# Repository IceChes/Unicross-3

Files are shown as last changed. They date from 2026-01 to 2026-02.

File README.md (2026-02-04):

# Unicross
Unicross is a highly reliable cross-gantry 3D printer built with accessible parts and simple design practices.



For up to date CAD: https://cad.onshape.com/documents/4eb1484887fc2987f4944e2c/w/5df6581cff3116f0fb19b47b/e/0f43dcdbef88a724da59cfd0

This project is IN PROGRESS and subject to change at any time without notice.

### Features:
- 180mm printing area
- Printable in PETG
- Direct drive extruder and Bambu hotend
- Accessible BOM
- Assembly manual
- Quality part cooling
- Self replicating
- Open source hardware (through Onshape)
- Runs Klipper

### Coming eventually:
- Prusaslicer configs
- Klipper configs
- Wiring guide

# What's the point?
My Unicross 3 build, after ironing out some first-assembly issues, has never broken. Cross gantry 3D printers are known for their speed, yes, but the dead-simple geometry and the overbuilt mechanics of the kinematics system in general makes it an unbelievably reliable basis for a 3D printer. 

# Sourcing components
This isn't a Voron or something that you can just buy a kit for, but the components are really easy to get. Due to tariffs, however, I cannot accurately estimate a price for this machine. 

I do not recommend spending more than $350 to build this thing. It's just not worth it, even with the reliability. I implore you to do your own shopping and come to your own conclusions.

**Cost cutting tips:** 
- If you have a couple old Monoprice Maker Selects lying around (this is a surprisingly common situation?) then the price drops dramatically as many of the motion components (and the bed!) can be repurposed.
- Both X motors must be identical, and both Y motors must be identical. However, the X motors and Y motors don't have to be the same as each other.
- The entire electronics enclosure can be PLA.
- There's a huge list of compatible beds to choose from. Pick any one that will fit! Alternatively, pop into Onshape and design your own - the design is uncomplicated.
- The power supply mounts are designed for an LRS-350-24 from meanwell. However, the Ender 3 power supply is exactly the same size, just thicker.
- Short on LM8LUUs? You can use regular LM8UUs for the Z axis with a small quality sacrifice, just not for the X/Y axes.

# Features, in detail
### X/Y axes
Unicross is based on linear rods due to their low cost and mechanical simplicity. They aren't super rigid or anything, so the machine isn't terribly fast, but it's cheap and it works. The belts are regular GT2 belts.

### Z axis
The Z axis is a single-motor dual-screw system driven with a belt. This isn't perfect, but it gets Z axis quality that's up to my standards. 

### Electronics
It has them. Requires bending pins for assembly, but it's not actually that big of a deal.

### Toolhead
The toolhead is a very simple plastic brick, designed for simplicity and durability. There isn't much to say here. 

# Questions you may have
### I don't like something. Can it be changed?
Sure. Just copy the Onshape document or download the assembly STEP and make whatever changes you want. I would love if you'd also DM me @iceches on Discord and I'll see if I can implement it in the main repository.

### What can I print?
PLA, PETG, TPU without an enclosure. If you have an enclosure or you cover up the sides and top, ABS, ASA, and PA are also printable.

### What can't I print?
I have no idea. Every filament I've tried has worked.

### Are there any known issues with this design?
Certainly. The idler mounting is suboptimal, and the Z axis is imperfect. I was unable to fix these two issues, but you might be able to!

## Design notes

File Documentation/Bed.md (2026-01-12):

# Bed stuff 
Unicross 3 was originally designed to use the Kingroom KP3S bed. However, this printer is discontinued. Some alternatives have been offered instead.
- Kingroon KP3S: The original bed. The PID tuning will work out of the box.
- Custom Unicross: Custom 200W PCB bed. Gerber files included. See documentation below.
- Lerdge IX: 180mm bed from the little-known Lerdge IX printer. These are pretty cheap online.
- Monoprice: Monoprice Maker Select bed. Oversized, but very common. Uses 12 volts, however, so some PID tuning may be in order.

### Notes
The BOM assumes that you have ALL necessary mounting hardware and electronics. This means that if you are using, for example, the custom Unicross bed, you will need to supply your own long M3 bolts, springs, and knobs. 
All Unicross beds MUST be able to be leveled using springs.
Also, remember to print the cooresponding mounts for whatever bed you pick.

### Custom bed
The custom Unicross bed is not a particularly economical option due to the cost of one-off manufacturing of boards this large. However, it is by far the most powerful bed.

The PCB has been designed for 1oz copper. It should be ordered in as thick of an FR4 substrate as reasonable, or ~3mm aluminum substrate. 

Kicad and gerber files are attached in the /Files/Bed Files/ directory.

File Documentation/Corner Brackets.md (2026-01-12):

# Unicross Corner Brackets
Unicross uses a variety of 90-degree angle corner brackets to secure various parts of the machine. The user is given the choice between large and small brackets.

There are a total of 12 corner brackets.
- 4 for the base. They support the vertical extrusions at the front of the machine.
- 4 for the sides. They support the Z axis side rails.
- 4 for the top. They brace the top of the printer.

Of these, the 8 for the base and the sides can be large or small. The top brackets **MUST** be large brackets, or you will risk the machine being pulled out of square, resulting in all kinds of artifacts.

The 4 for the base _should_ be large brackets, as this will help give stability to the entire machine. The back side of the printer is not as rigid as the front due to its construction, but further reinforcing the front will still help the back quite a lot.

The 4 for the side rails can be large or small. Large brackets will marginally improve rigidity, but small ones save you a couple bolts. 

TL;DR I recommend printing 8 large corner brackets and 4 small ones.

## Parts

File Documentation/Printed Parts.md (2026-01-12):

# Unicross 3 Printed Parts guide
This is an extensive guide on printing the Unicross 3 components. 

---

# Print settings
Assuming 0.3mm layer height and 0.4 nozzle.

### Minimal structural settings for ABS
- 3 walls
- 4 top layers
- 4 bottom layers
- 20% 3D infill

### Minimal structural settings for PETG
- 5 walls
- 6 top layers
- 6 bottom layers
- 25% 3D infill

### Nonstructural settings for all filaments
- 3 walls
- 3 top layers
- 2 bottom layers
- 10% any infill

I highly recommend enabling the option in your slicer that adds a sparse top layer before the true top layer printing starts. This will dramatically improve panel quality.

**Settings for other filaments are up to the user's discretion to decide.**

### Bed Mounts (all)
- Quantity: 2 (of your selected mount)
- Settings: At least minimal structural settings
- Filament: Recommended ABS or PETG, or another non-creeping filament resistant to 70C or so

### Jigs (all)
- Quantity: 1 of each item
- Settings: Nonstructural
- Filament: Any

Jigs are disposable.

### Panels - all except screw plates and fan retainer
- Quantity: 1 of each item
- Settings: Nonstructural
- Filament: Any

### Panels - fan retainer
- Quantity: 1
- Settings: 100% infill solid
- Filament: Any

### Panels - screw plates
- Quantity:
  - 4x 2mm-2x1
  - 2x 2mm-2x2
  - 2x 4mm-2x1
  - 2x 4mm-2x2
- Settings: 100% infill solid
- Filament: Any

### Toolhead - toolhead block
- Quantity: 1
- Settings: At least minimal structural settings
- Filament: Recommended ABS or PETG, or another non-creeping filament resistant to 70C or so

### Toolhead - toolhead hotend clamp
- Quantity: 1
- Settings: At least minimal structural settings
- Filament: Recommended ABS or PETG, or another non-creeping filament resistant to 70C or so

### Toolhead - BLTouch mount
- Quantity: 1
- Settings: 100% infill solid
- Filament: Any filament resistant to 70C

### Fastening plate
- Quantity: 11 recommended, but you can bolt these on in loads of places
- Settings: 100% infill solid
- Filament: Any non-creeping filament

### Front foot
- Quantity: 2
- Settings: At least minimal structural settings
- Filament: Any non-creeping filament

### IEC socket mount
- Quantity: 1
- Settings: Nonstructural
- Filament: Any

### Idler bracket
- Quantity: 4
- Settings: 100% infill solid
- Filament: Any non-creeping filament

### Idler cover
- Quantity: 4
- Settings: At least minimal structural settings
- Filament: Any

### Large corner bracket
- Quantity: See bracket guide
- Settings: 100% infill solid
- Filament: Any non-creeping filament

### Long mount
- Quantity: 2
- Settings: At least minimal structural settings
- Filament: Recommended ABS or PETG, or another non-creeping filament resistant to 70C or so

### PSU fan duct (optional part)
- Quantity: 1
- Settings: Nonstructural
- Filament: Any

### Rear foot
- Quantity: 2
- Settings: At least minimal structural settings
- Filament: Any non-creeping filament

### Rod block with zip tie
- Quantity: 1
- Settings: At least minimal structural settings
- Filament: Any non-creeping filament

### Rod block
- Quantity: 3
- Settings: At least minimal structural settings
- Filament: Any non-creeping filament

### Short mount
- Quantity: 2
- Settings: At least minimal structural settings
- Filament: Recommended ABS or PETG, or another non-creeping filament resistant to 70C or so

### Small corner bracket
- Quantity: See bracket guide
- Settings: 100% infill solid
- Filament: Any non-creeping filament

### Z motor mount
- Quantity: 1
- Settings: At least minimal structural settings
- Filament: Recommended ABS or PETG, or another non-creeping filament resistant to 70C or so

### Z rod top support
- Quantity: 4
- Settings: At least minimal structural settings
- Filament: Any non-creeping filament

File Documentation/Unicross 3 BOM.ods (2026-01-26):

Framing and Hardware
Part | Description | Quantity | Notes
350mm 2020 extrusion | Primary frame component | 14 | You can also buy 5 meters and cut it into 14 sections, with an extra 100mm piece.
M5x10 button head cap screw |  | 150 | You'll have some extra of all major hardware components, these are approximations.
M5 T nut |  | 150
M3x10 button head cap screw |  | 75
M3 square nut |  | 75
M3x12 button head cap screw | Extruder + fan screws | 4 | Exact quantity. Specifically to mount the sherpa mini and the hotend fan. May come included with both!
M4x8 button head cap screw | PSU screws | 4 | Exact quantity.
M3x25 button head cap screw | Tensioner + hotend screws | 6 | Exact quantity. Used for mounting the tensioners and also the hotend. You may get 2 with your hotend.
M5x25 button head cap screw | Idler retaining bolts | 4 | Exact quantity.
Electronics
Part | Description | Quantity | Notes
Raspberry Pi model B | Any model-B Pi-shaped SBC | 1 | I use a Pi 4, but the SBC market is the wild west nowadays.
BTT SKR Pico | Mainboard | 1
Stepper motor | NEMA17 of ~40mm in length | 5 | I do not recommend any particular motor, use spares if you have them. HOWEVER the XY motors should all be the same.
Stepper cable |  | 5 | Don't forget!
Stepper splitter | Run motors in parallel | 2
Meanwell LRS-350-24 | Generic power supply | 1 | If you have an Ender PSU or whatever that works too, but it won't sit flush with the panels.
IEC 320 switched + fused socket | Power plug | 1 | You want the kind with the mounting holes on the top and bottom, not the left and right.
Z Axis
Part | Description | Quantity | Notes
8x250mm linear rod | Z axis rods | 4
30T GT2 pulley | Z axis pulleys | 2
~730mm GT2 belt loop | Z belt | 1 | Exact belt length is 727mm, but the belt should be slightly longer.
250mm T8 leadscrew | Z screw | 2 | PLEASE try to get straight screws.
T8 nut | Z screw nut | 2 | The round ones!
608 bearing | Screw bearings | 2 | Yep. Those.
Bed |  | 1 | Read Bed.md for information
X and Y Axes
Part | Description | Quantity | Notes
8x300mm linear rod | Gantry and cross rods | 6
20T GT2 pulley | Primary pulleys | 4 | All 20T GT2 hardware can be substituted for 16T if you'd like.
20T GT2 idler | Primary idlers | 4
GT2 belt |  | 4x700mm
LM8LUU bearing | Linear bearings | 10 | 4 of these will be used on the Z axis, and 2 will be used on the toolhead.
Toolhead
Part | Description | Quantity | Notes
Bambu Lab X/P/A hotend | Hotend | 1
2510 axial fan | Hotend cooling fan | 1 | Try to get one included with the hotend, but make sure it has a normal connector.
4010 blower fan | Part cooling fan | 3 | You'll need an extra for electronics cooling.
BLTouch-style probe | Probe | 1 | If it ain't broke...
Sherpa mini | Extruder | 1
PTFE tubing |  | ~40mm | Cut to length during head assembly.

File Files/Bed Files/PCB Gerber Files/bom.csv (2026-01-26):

Designator | Footprint | Quantity | Value | LCSC Part #
J1, J2 | SolderWire-1.5sqmm_1x01_D1.7mm_OD3.9mm | 2 | Conn_01x01

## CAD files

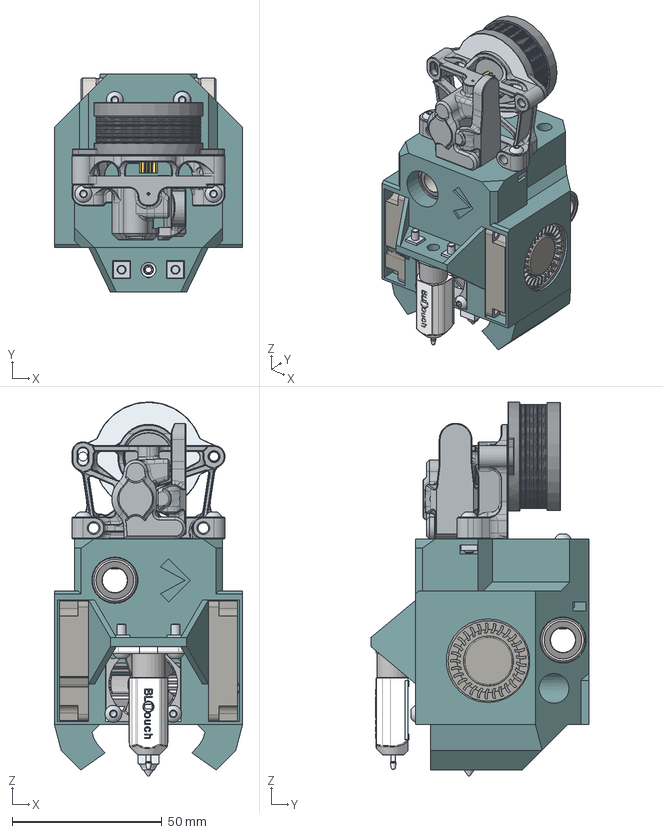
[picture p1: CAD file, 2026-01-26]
Files/Assemblies/Toolhead.step
63.0 x 73.0 x 125.1 mm
Socket button head screw M3x0.5 x 12 x 2
4010 Blower x 2
Square thin nut grade B M3x0.5 x 8
Socket button head screw M3x0.5 x 10 x 6
Socket button head screw M3x0.5 x 20 x 2
25MM SUNON FAN x 2
Sherpa Mini
Hotend
Toolhead Block
LM8LUU x 2
ProbePin
Housing
BreadBoard
CoilBL

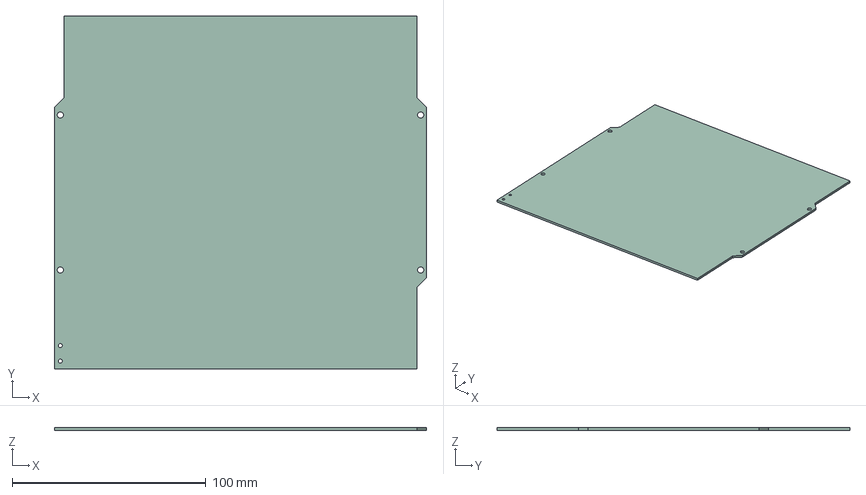
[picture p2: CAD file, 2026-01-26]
Files/Bed Files/Unicross Bed.step
192.0 x 182.0 x 1.60 mm

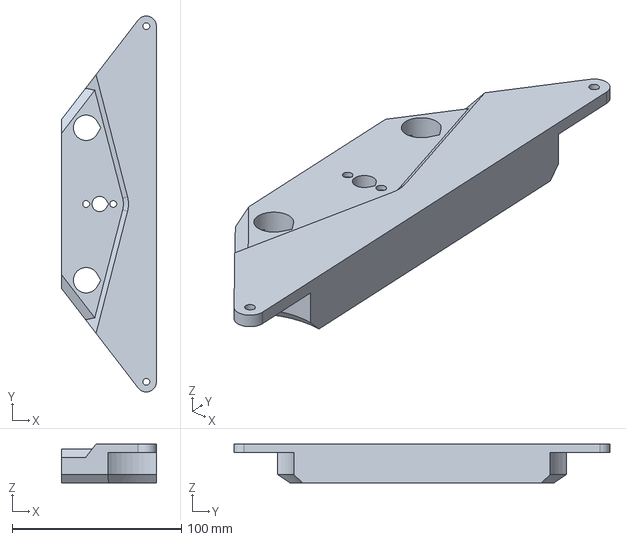
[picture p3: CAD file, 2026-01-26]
Files/Individual Part STEPs/Bed Mounts/Bed Mount - Monoprice.step
56.0 x 222.0 x 23.0 mm

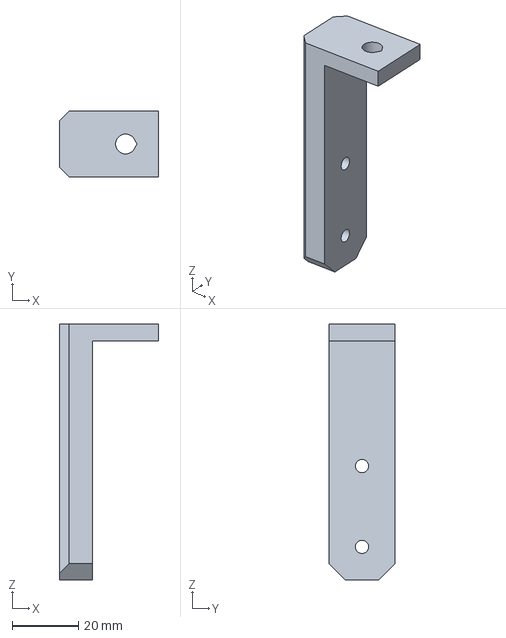
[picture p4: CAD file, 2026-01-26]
Files/Individual Part STEPs/Jigs/Jigs - Drill Jig.step
30.0 x 20.0 x 77.3 mm

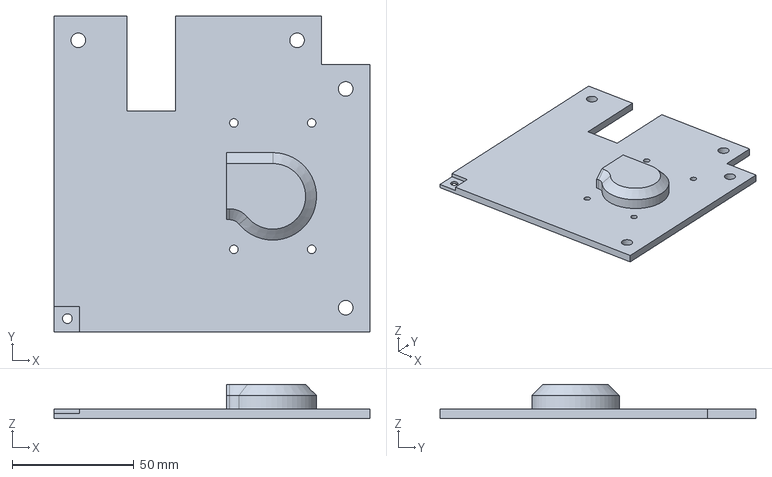
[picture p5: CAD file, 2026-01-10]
Files/Individual Part STEPs/Panels/Back Right Top Plate.step
130.0 x 130.0 x 14.0 mm

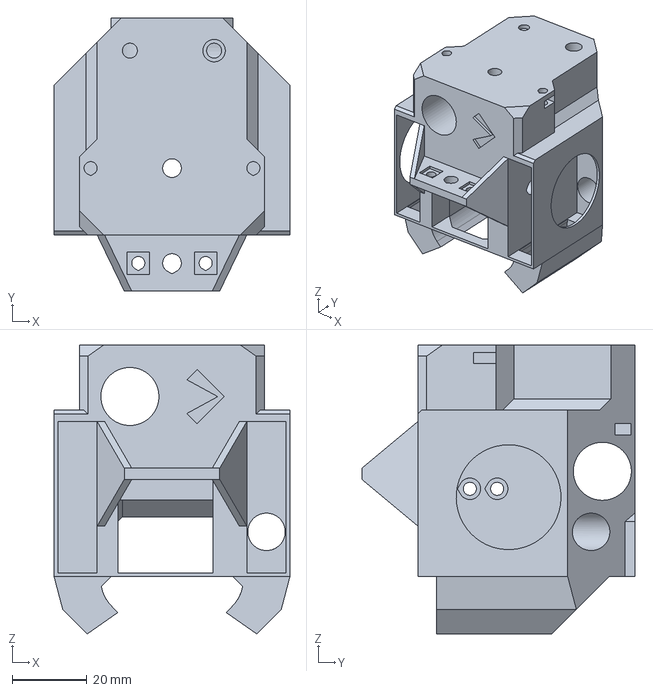
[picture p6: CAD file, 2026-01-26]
Files/Individual Part STEPs/Toolhead Block.step
63.0 x 73.0 x 77.2 mm

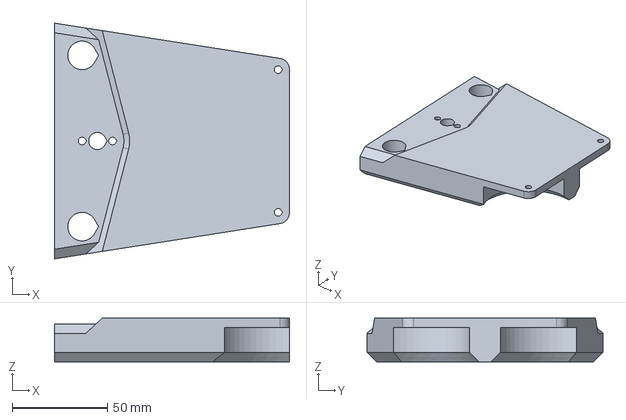
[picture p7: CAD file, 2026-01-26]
Files/Individual Part STEPs/Bed Mounts/Bed Mount - Lerdge IX.step
123.5 x 123.9 x 23.0 mm

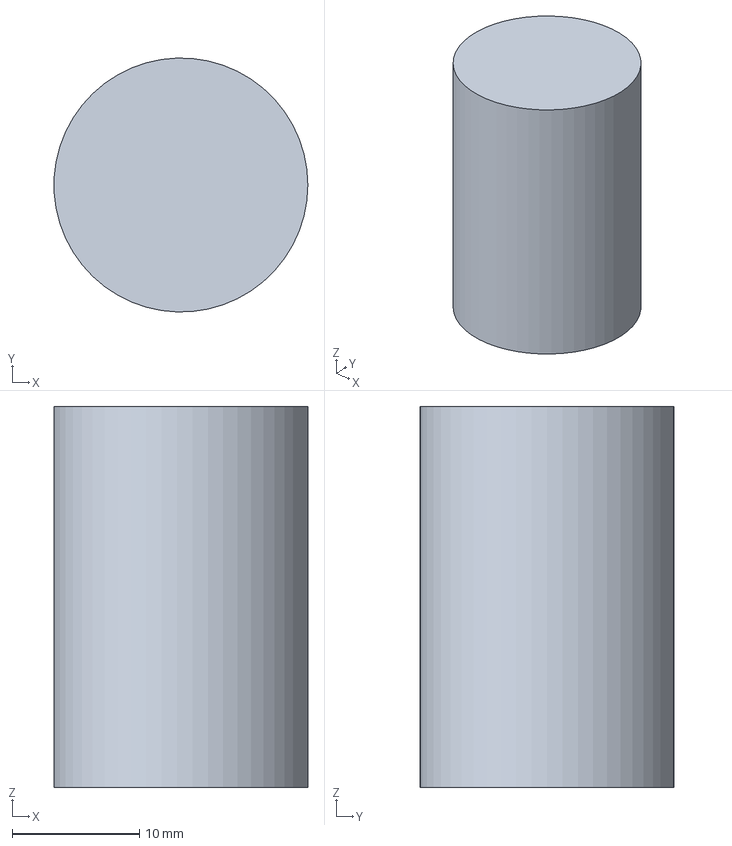
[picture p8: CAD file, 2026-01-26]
Files/Individual Part STEPs/Jigs/Jigs - Bearing Tool.step
20.0 x 20.0 x 30.0 mm

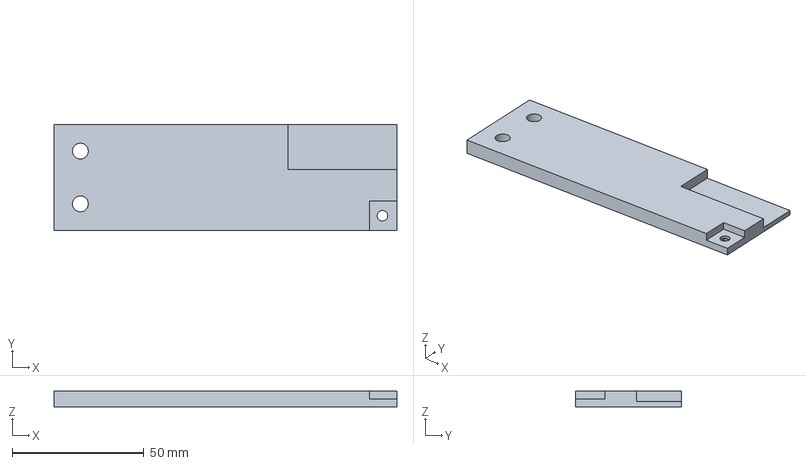
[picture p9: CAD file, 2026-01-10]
Files/Individual Part STEPs/Panels/Front Left Bottom Plate.step
130.0 x 40.0 x 6.00 mm

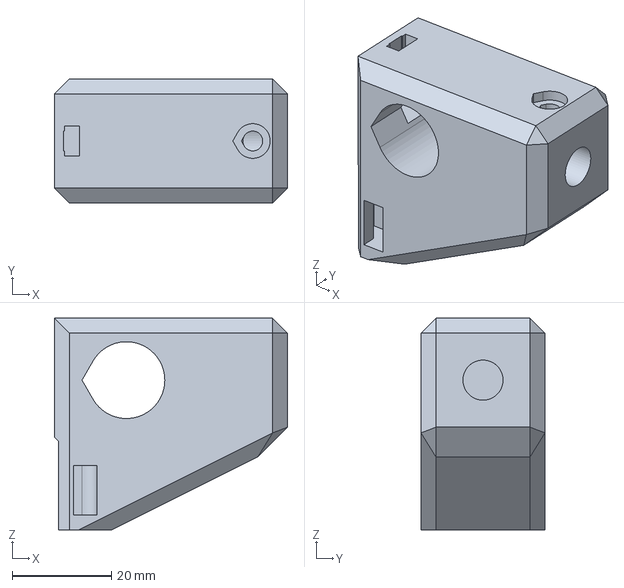
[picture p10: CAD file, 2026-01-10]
Files/Individual Part STEPs/Rod Block.step
47.0 x 25.0 x 42.7 mm

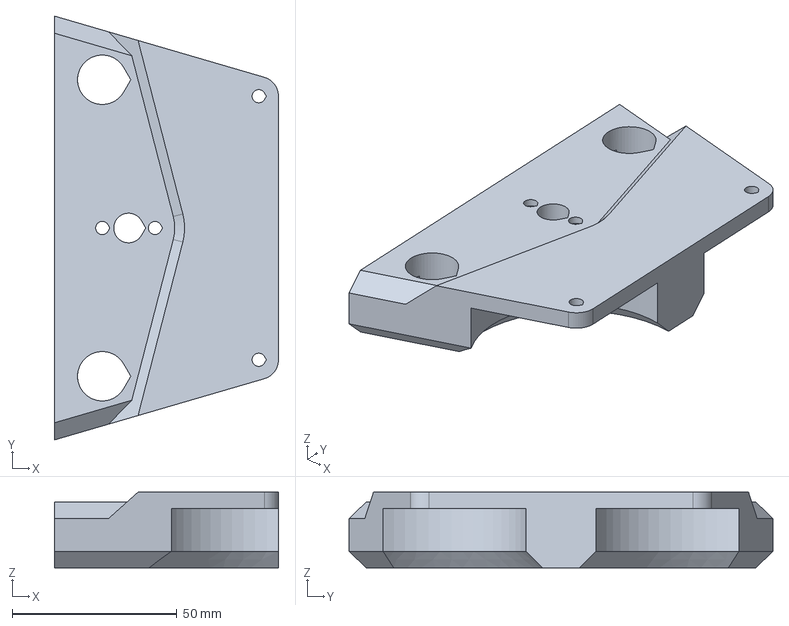
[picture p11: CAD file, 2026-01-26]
Files/Individual Part STEPs/Bed Mounts/Bed Mount - Custom Unicross.step
68.0 x 128.7 x 23.0 mm

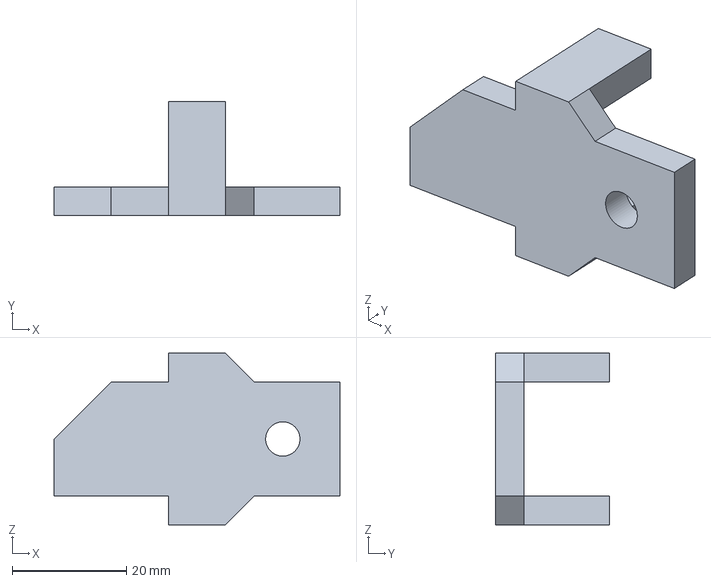
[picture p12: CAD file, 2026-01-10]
Files/Individual Part STEPs/Idler Cover.step
50.0 x 20.0 x 30.0 mm

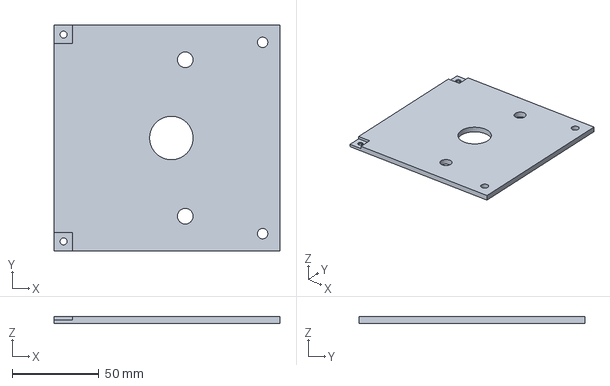
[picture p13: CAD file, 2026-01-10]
Files/Individual Part STEPs/Panels/Right Mid Top Plate.step
130.0 x 130.0 x 4.00 mm

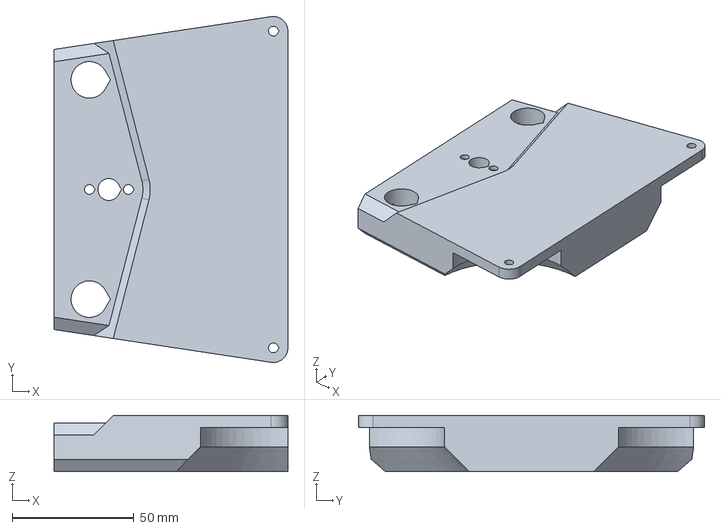
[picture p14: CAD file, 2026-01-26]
Files/Individual Part STEPs/Bed Mounts/Bed Mount - KP3S.step
96.0 x 142.0 x 23.0 mm

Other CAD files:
Files/Individual Part STEPs/Fastening Plate.step
Files/Individual Part STEPs/Panels/Front Right Top Plate.step
Files/Individual Part STEPs/Panels/Left Mid Top Plate.step
Files/Individual Part STEPs/Small Corner Bracket.step
Files/Bed Files/Unicross Bed.dxf
Files/Individual Part STEPs/Front Foot.step
Files/Individual Part STEPs/IEC Socket Mount.step
Files/Individual Part STEPs/Idler Bracket.step
Files/Individual Part STEPs/Large Corner Bracket.step
Files/Individual Part STEPs/Long Mount.step
Files/Individual Part STEPs/PSU Fan Duct.step
Files/Individual Part STEPs/Panels/2x1 Screw Plate - 2mm.step
Files/Individual Part STEPs/Panels/2x1 Screw Plate - 4mm.step
Files/Individual Part STEPs/Panels/2x2 Screw Plate - 2mm.step
Files/Individual Part STEPs/Panels/2x2 Screw Plate - 4mm.step
Files/Individual Part STEPs/Panels/Back Left Bottom Plate.step
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

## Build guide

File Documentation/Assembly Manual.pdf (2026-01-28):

You’re going to need to prep 4 extrusions before use. Find them, an M5 tap, a 3mm drill bit, and the drill jig.

Tap the hole at the end. Repeat for the other 3.

Attach the jig to the end of an extrusion and drill a hole using the top hole of the jig. Repeat for the other 3.

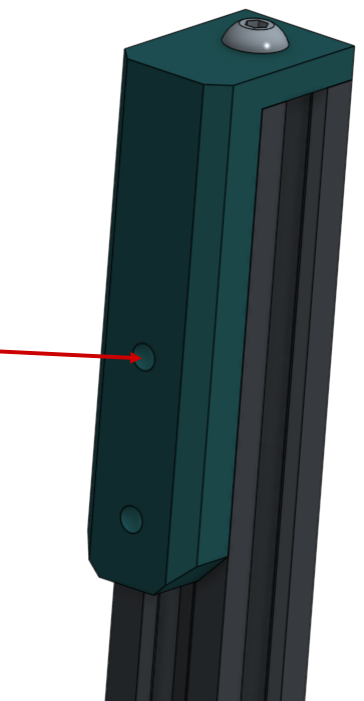
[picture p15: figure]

Attach the jig again at a 90 degree offset and drill through the bottom hole. Repeat for all 3.

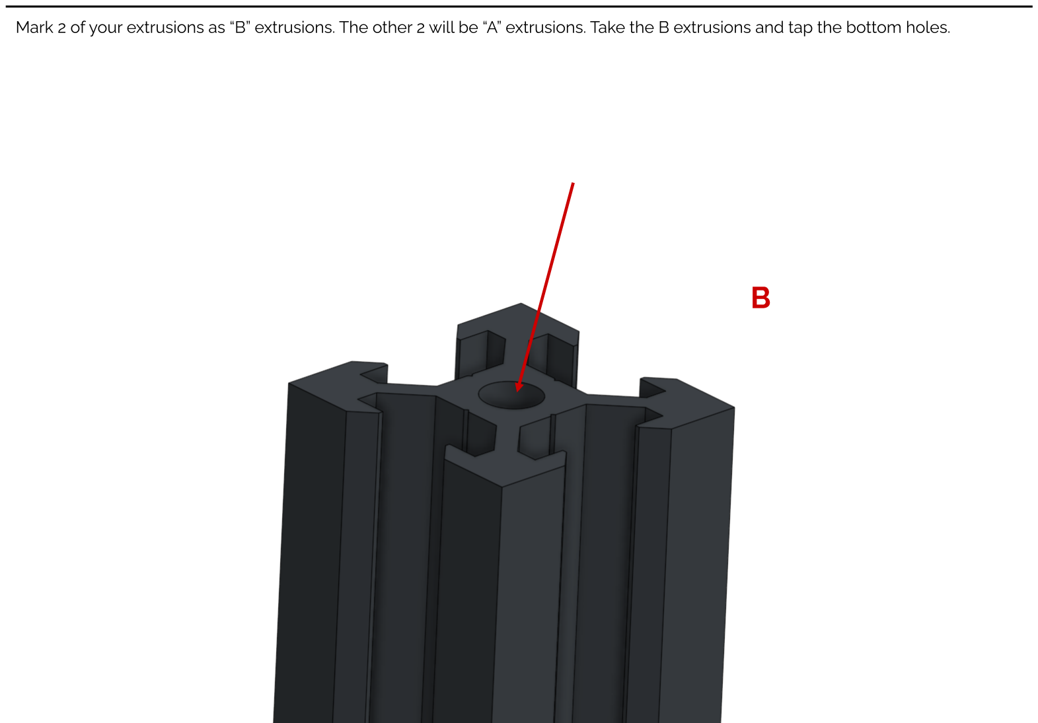
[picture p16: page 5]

Mark 2 of your extrusions as “B” extrusions. The other 2 will be “A” extrusions. Take the B extrusions and tap the bottom holes.

B

Mark 2 of your extrusions as “B” extrusions. The other 2 will be “A” extrusions. Take the B extrusions and tap the bottom holes.

B

M3 square nut | 4
M3x10 screw | 4
Rear left bottom plate | 1
Rear foot | 1

M3 square nut | 4
M3x10 screw | 4
Rear right bottom plate | 1

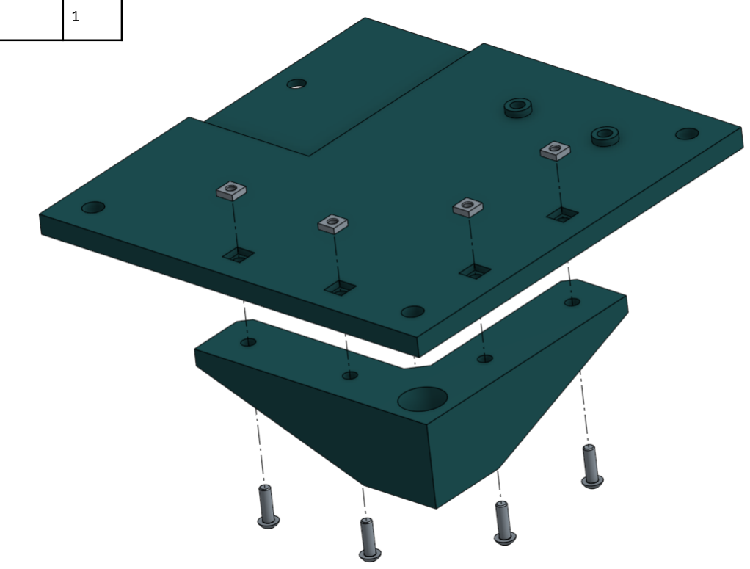
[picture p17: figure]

Rear foot | 1

2020 extrusion | 4 | Arrange 3 extrusions edge to edge on a flat surface in this orientation.

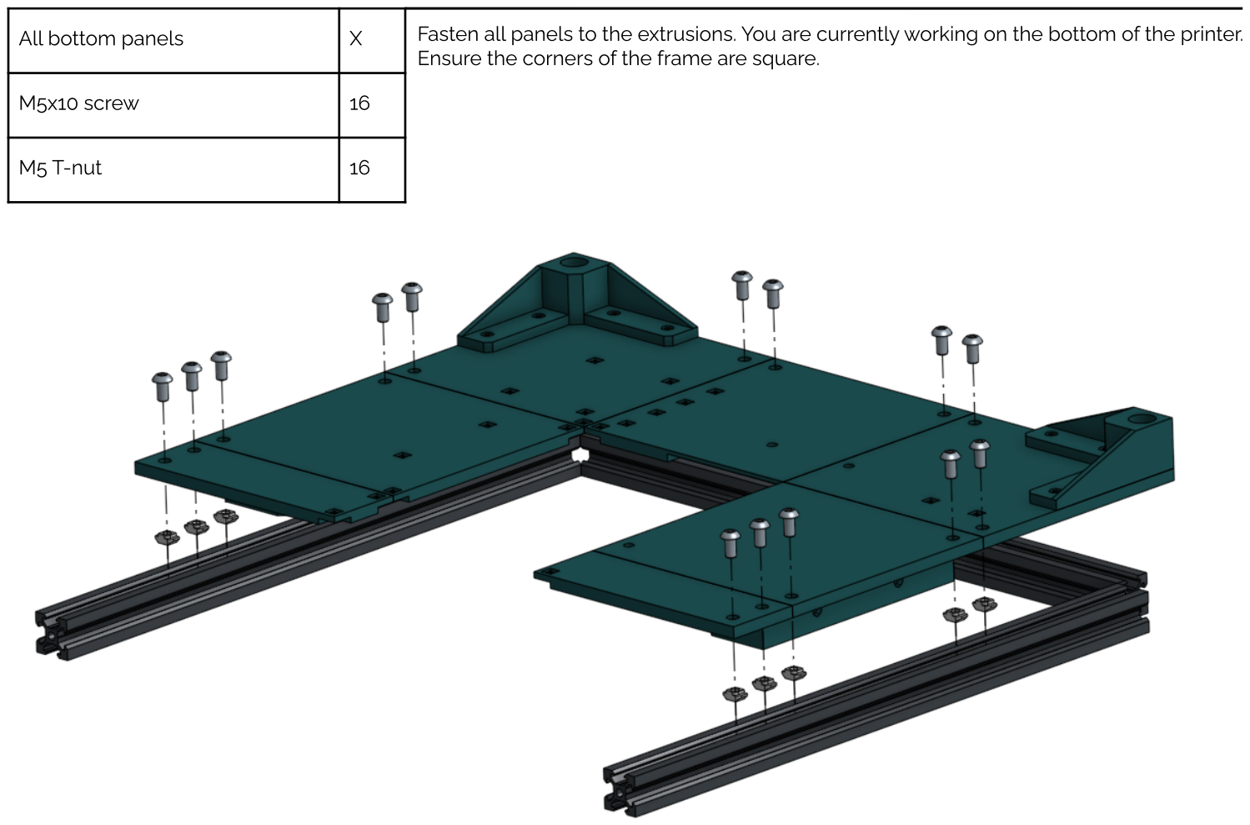
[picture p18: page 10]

Fasten all panels to the extrusions. You are currently working on the bottom of the printer. Ensure the corners of the frame are square.

All bottom panels | X
M5x10 screw | 16
M5 T-nut | 16

Using the screw plates, fasten the center bottom plate and front bottom plate to the rest of the array of plates.

M3x10 screw | 12
M3 square nut | 12
2x1-4mm screw plate | 2
2x2-4mm screw plate | 2
Center bottom plate | 1
Front mid bottom plate | 1

To fully fasten the bracket plates, slide T nuts into the extrusion channels behind them and tighten screws into the nuts inside the large counterbores in the side. This needs to be done on both sides.

M5x10 screw
4

M5 T nut
4

2020 corner bracket | 2
M5x10 screw | 2
M5 T nut | 2

2020 extrusion | 1
M5x10 screw | 2
M5 T nut | 2

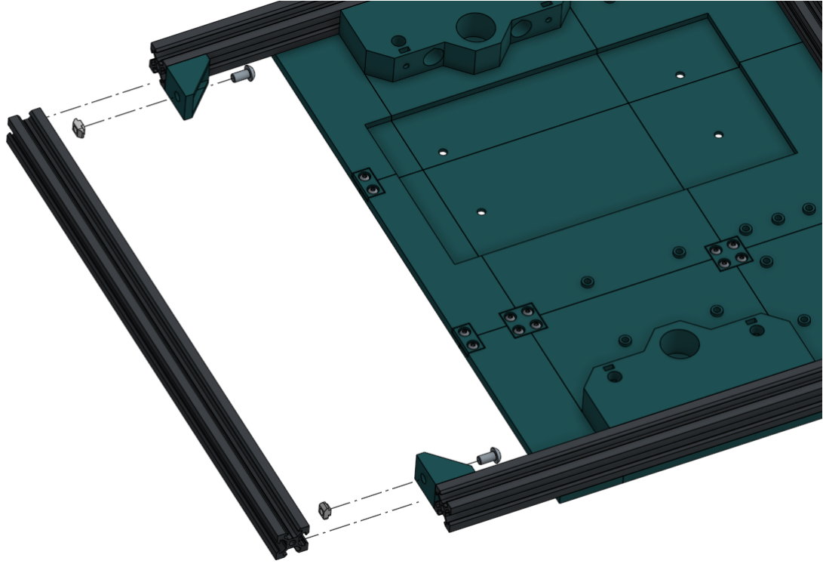
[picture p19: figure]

Front foot | 2
M5x10 screw | 8
M5 T nut | 8

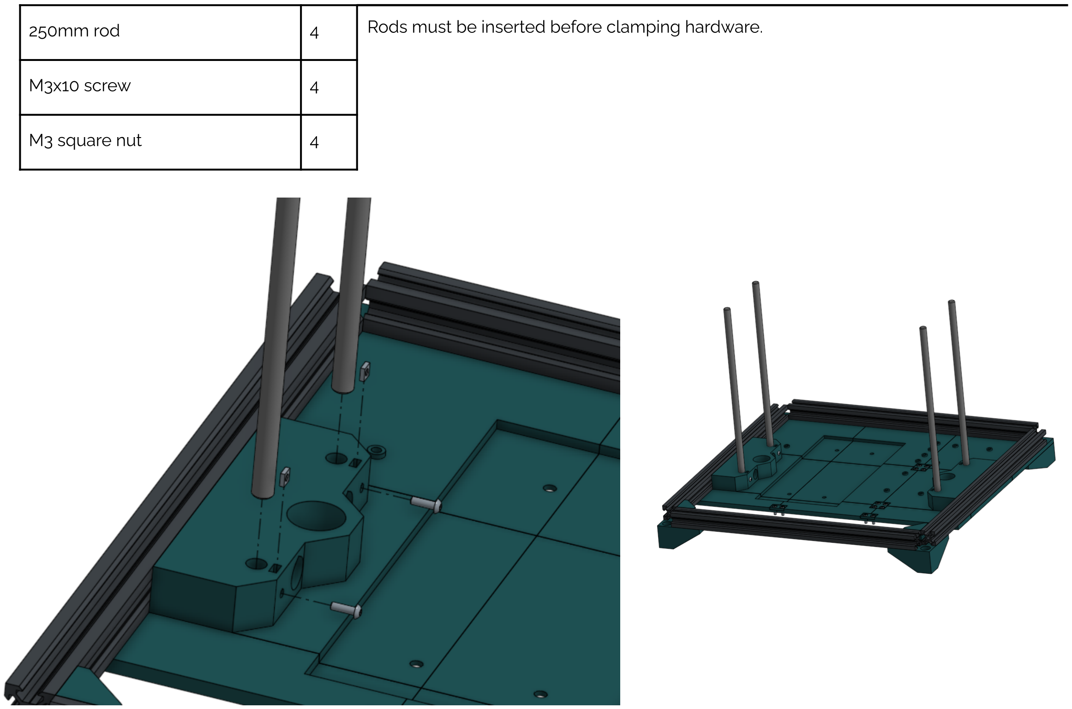
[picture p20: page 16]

250mm rod | 4 | Rods must be inserted before clamping hardware.
M3x10 screw | 4
M3 square nut | 4

Power supply | 4 | Terminals should face toward the back of the printer.
M4x6 screw | 4

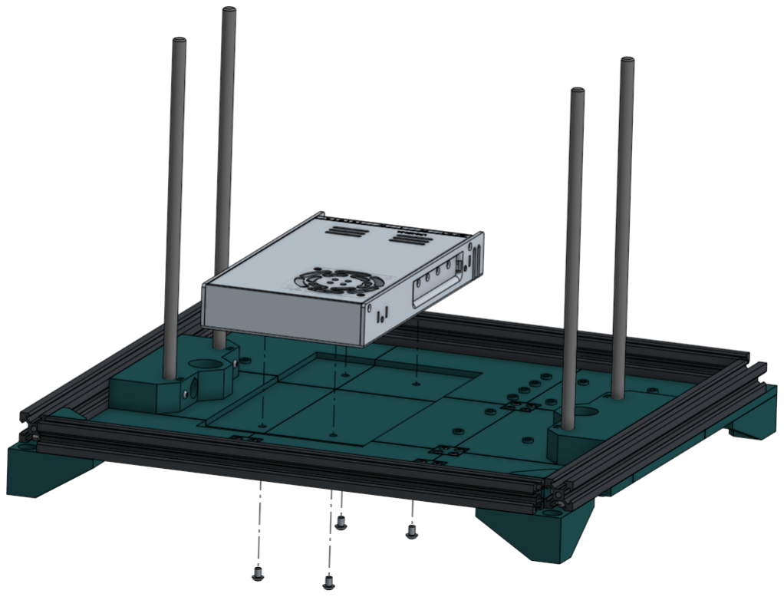
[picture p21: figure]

All listed electronics should be attached. Only the Pi is pictured here. There are recesses for nuts on the bottom.

Parallel adapter | 2
Mainboard | 1
Pi | 1
M3x10 screw | 12
M3 square nut | 12

Step 12.5: At this time, connect the mainboard to the Pi using the mainboard cable.

Unfortunately, the cable will not fit underneath the electronics enclosure lid by default. You will need to either install a right-angle header on the Pi, or bend the pins off to the side. The method I used was to plug the connector into the Pi and then bend the pins by pushing on the connector. This ensures an even bend, and helps ensure stable electrical connection.

Also at this time connect the mainboard to the stepper adapters using the tiny included cables, and wire up the power system with the exception of attaching the power socket (simply attach loose cables to the power input on the power supply). Plug in all stepper cables, all toolhead cables, and all bed wires.

At the end of this step, everything except the power socket, stepper motors, and electronics fan should be wired up. The bed and the toolhead should be laying off to the side. Refer to step 12.5 in the wiring guide for assistance.

Tiny parallel adapter cable | 2
Mainboard cable | 1
Assorted 16awg wire | X

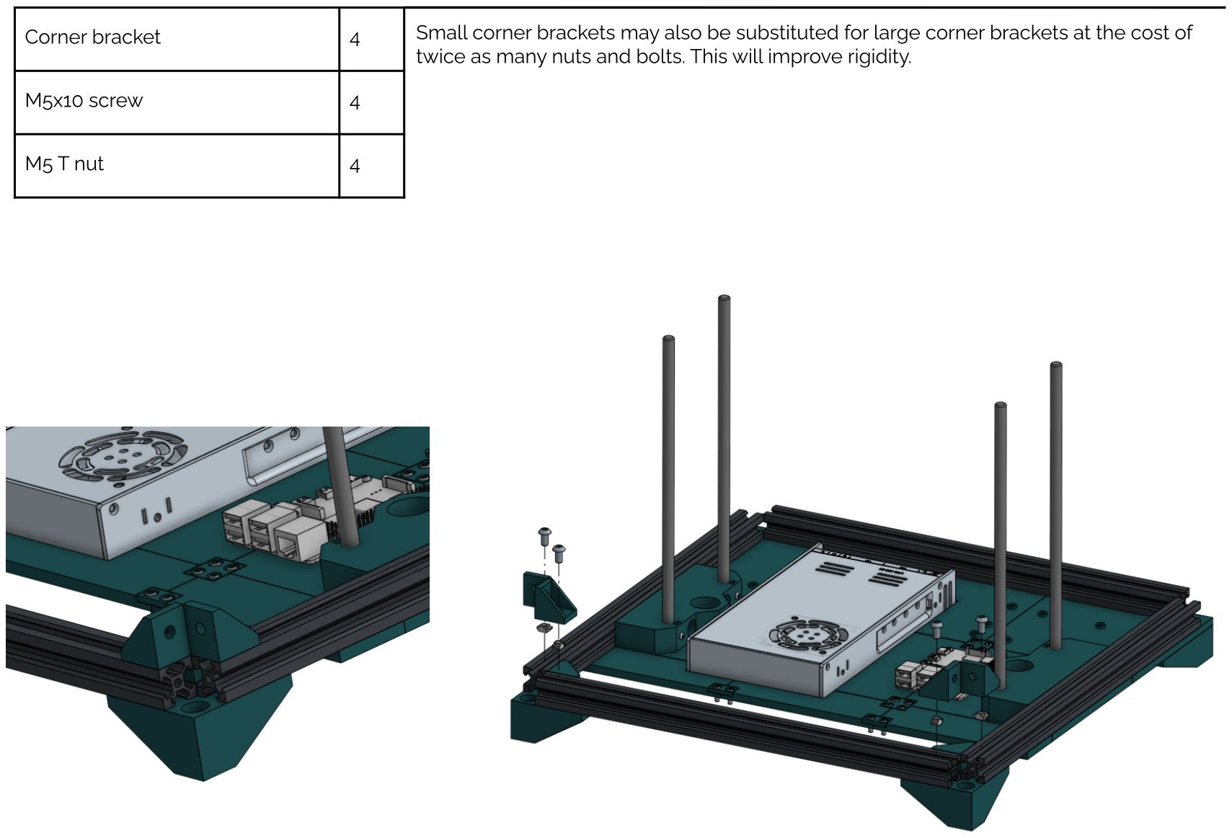
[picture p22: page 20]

Small corner brackets may also be substituted for large corner brackets at the cost of twice as many nuts and bolts. This will improve rigidity.

Corner bracket | 4
M5x10 screw | 4
M5 T nut | 4

If you used the larger corner brackets in the previous step, you’ll need twice as many nuts and bolts.

M5x10 screw | 4
M5 T nut | 4
Extrusion A | 2

A

A

Confirm your fitment of these extrusions.

Both “A” extrusions should have their “high” mounting holes facing forwards. The tops should have threads, and the bottoms should not.

A

# Threads

# No threads

A

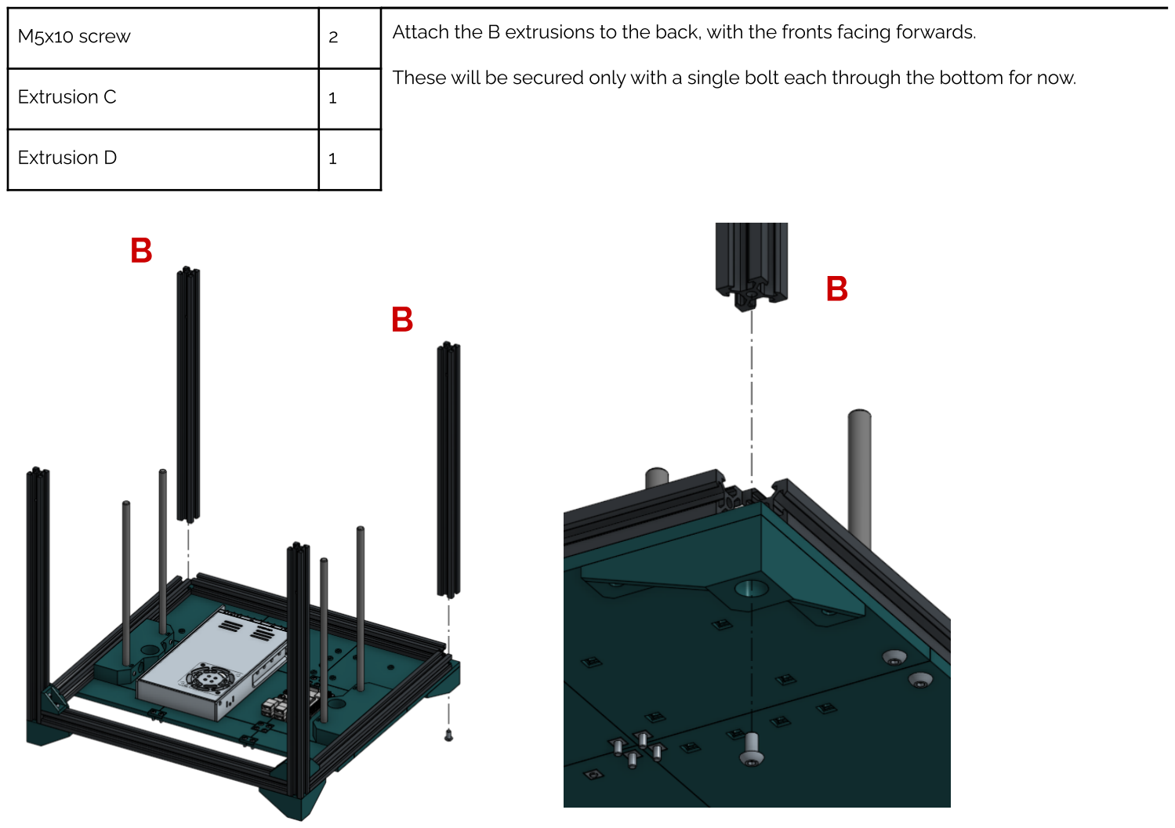
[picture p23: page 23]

Attach the B extrusions to the back, with the fronts facing forwards.

These will be secured only with a single bolt each through the bottom for now.

M5x10 screw | 2
Extrusion C | 1
Extrusion D | 1

B

B

B

Confirm your fitment of these extrusions.

The “B” extrusions should have their “high” mounting holes facing forwards. The tops should be threaded.

B

# Threads

Extrusions A and B hidden.

B

M5x10 screw | Pictured upside-down. 16
M3 T nut | 16
2x2 screw plate - 2mm | 2
2x1 screw plate - 2mm | 4

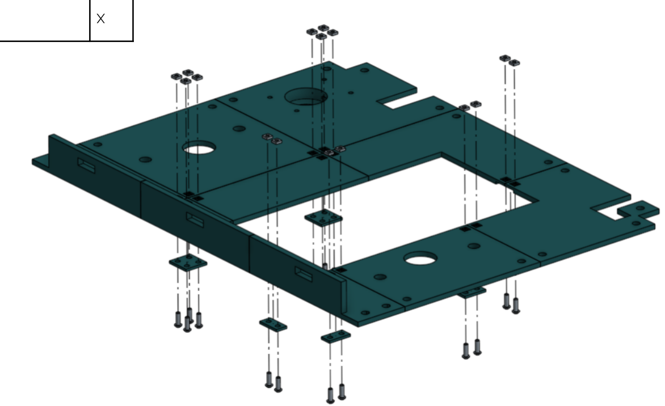
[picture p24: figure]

All top panels | X

M5x10 screw | 4 | The outlet should be facing to the left.
M3 T nut | 4
4010 blower fan | 1
4010 retainer | 4

Upright extrusions hidden for clarity. Lower the electronics cover onto the base of the printer. Plug in the electronics cooling fan (step 17 in wiring guide) and ensure printer cabling is passing through holes labeled below before tightening bolts.

M5x10 screw | 18
M5 T nut | 18
Assembled top panel | 1

# Z motor

# AC power X and Y motors

# Bed Toolhead

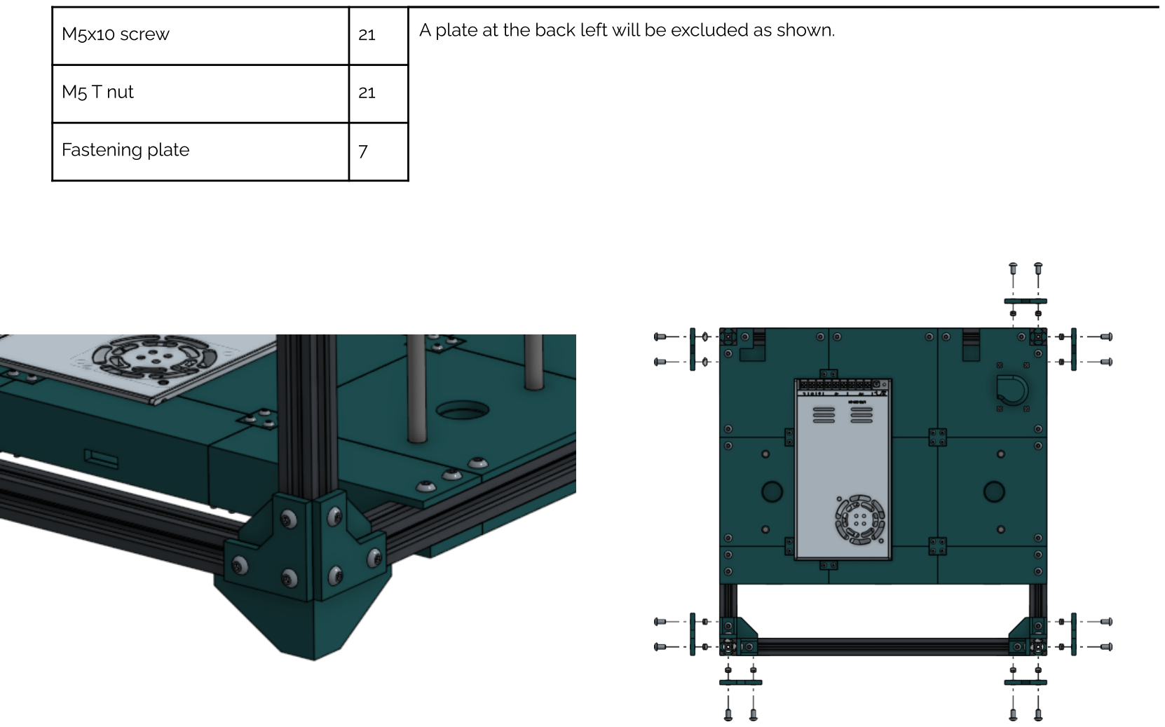
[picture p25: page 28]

M5x10 screw | 21 | A plate at the back left will be excluded as shown.
M5 T nut | 21
Fastening plate | 7

M3x10 screw | 2
M3 square nut | 2
Socket plate | 1
Power socket | 1

At this time connect the power socket to the loose power wires. Ensure safe insulation with heat shrink, there is no shroud or cover for the live wires provided.

M5x10 screw | 3
M5 T nut | 3
Assembled socket | 1

Drop the Z axis leadscrews into the bearings in the base of the machine. This will be a very loose fit for now.

Leadscrew
2

Z motor mount | Loosely fasten the Z axis motor mount to the front rail of the machine. 1
M5x10 screw | 5
M5 T nut | 5

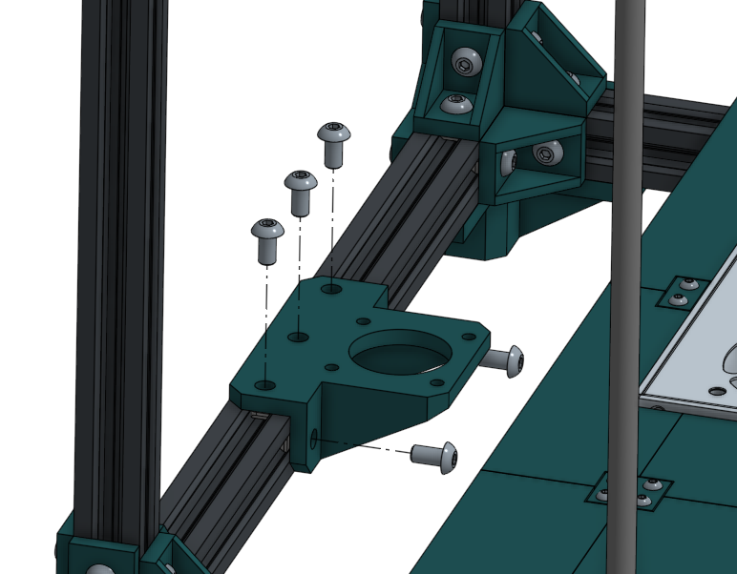
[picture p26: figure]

Z motor | Remember to plug the cable in. 1
M3x10 screw | 4

Install the Z axis idlers and belt. It should be a loose fit. Make sure the belt path is level.

The belt will be tightened once the Z axis is mostly together.

Z belt | 1
30T Z idler | 2

For the following steps, only one bed mount will be shown for clarity. Both must be assembled.

M3x10 screw | 4
M3 square nut | 4
Bed mount | 2

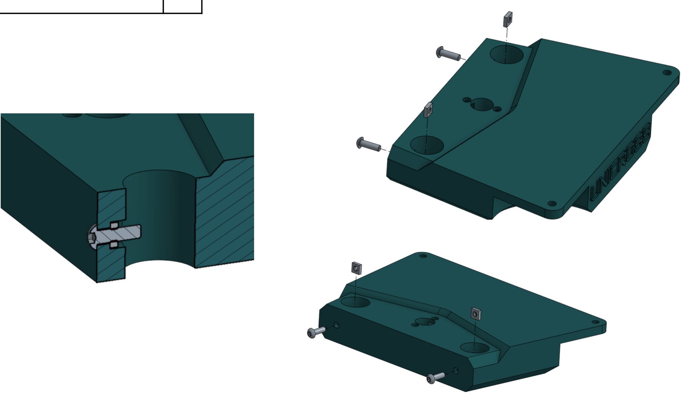
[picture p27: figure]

LM8LUU bearing | 4 | Install and clamp down linear bearings.
Bed mount | 2

T8 nut | 2
M3x10 screw | 4

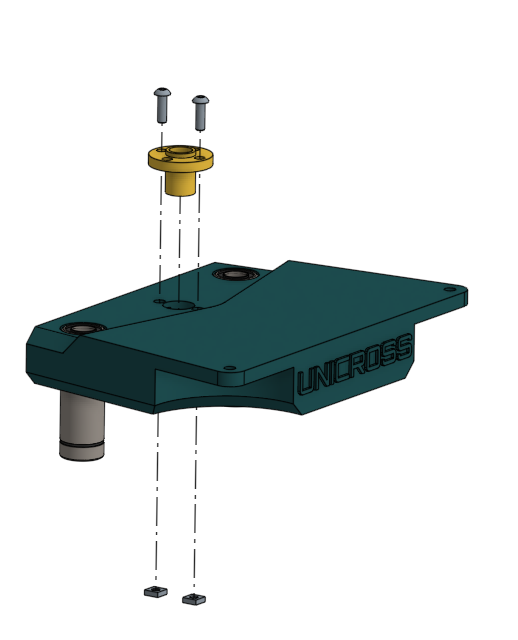
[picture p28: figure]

M3 square nut | 4
Bed mount | 2

Install the bed. This step varies depending on the bed you’re using, and you might have to provide your own screws and other hardware.

Bed | 1
Bed mount | 2

Lower the bed onto the printer, aligning the rods and screws. KEEP IT AS LEVEL AS POSSIBLE.

Assembled bed | 1
Printer assembly | 1

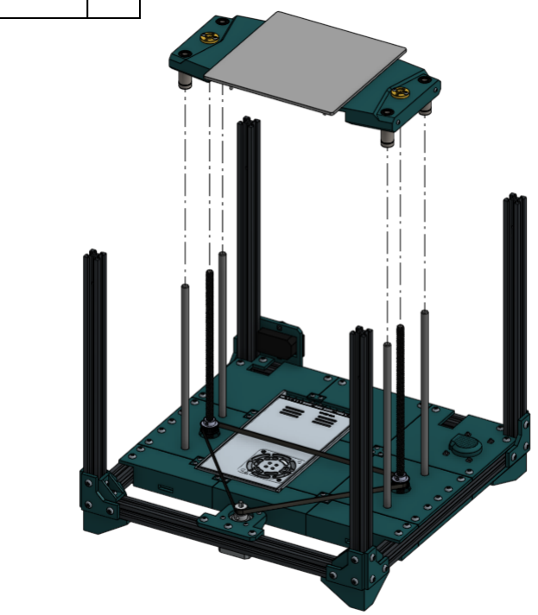
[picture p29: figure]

Pull the Z belt tight by sliding the Z axis motor mount to the left or right. If it does not slide easily, loosen the bolts more.

When the belt is reasonably tight, tighten the Z axis motor mount bolts to lock it in place. Do not over-tighten the belt.

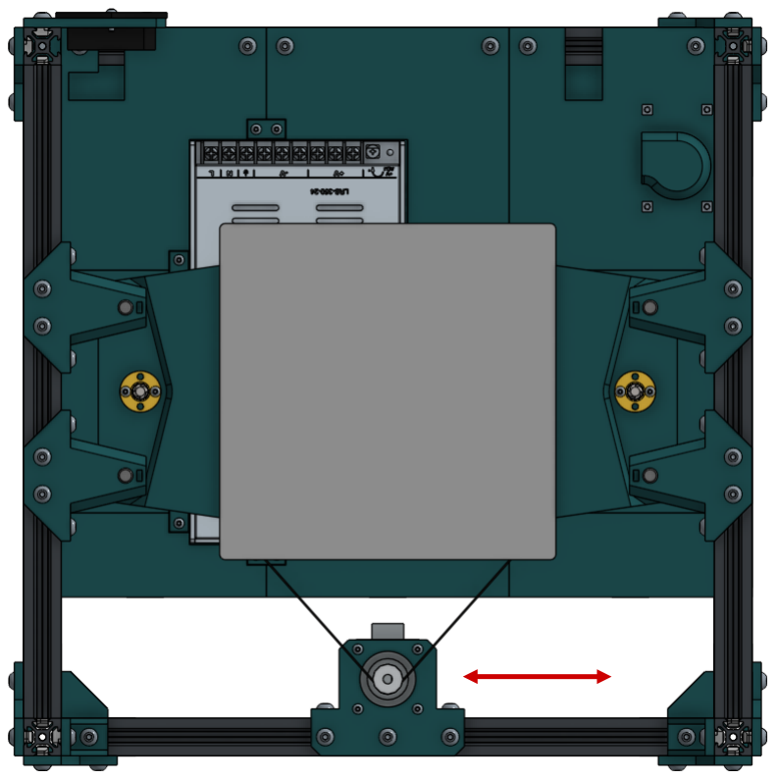
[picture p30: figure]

Build 2 of these. You can substitute the small corner brackets for large ones if you want, but there’s not much reason to here.

2020 extrusion | 2
Corner bracket | 4
M5x10 screw | 4
M5 T nut | 4

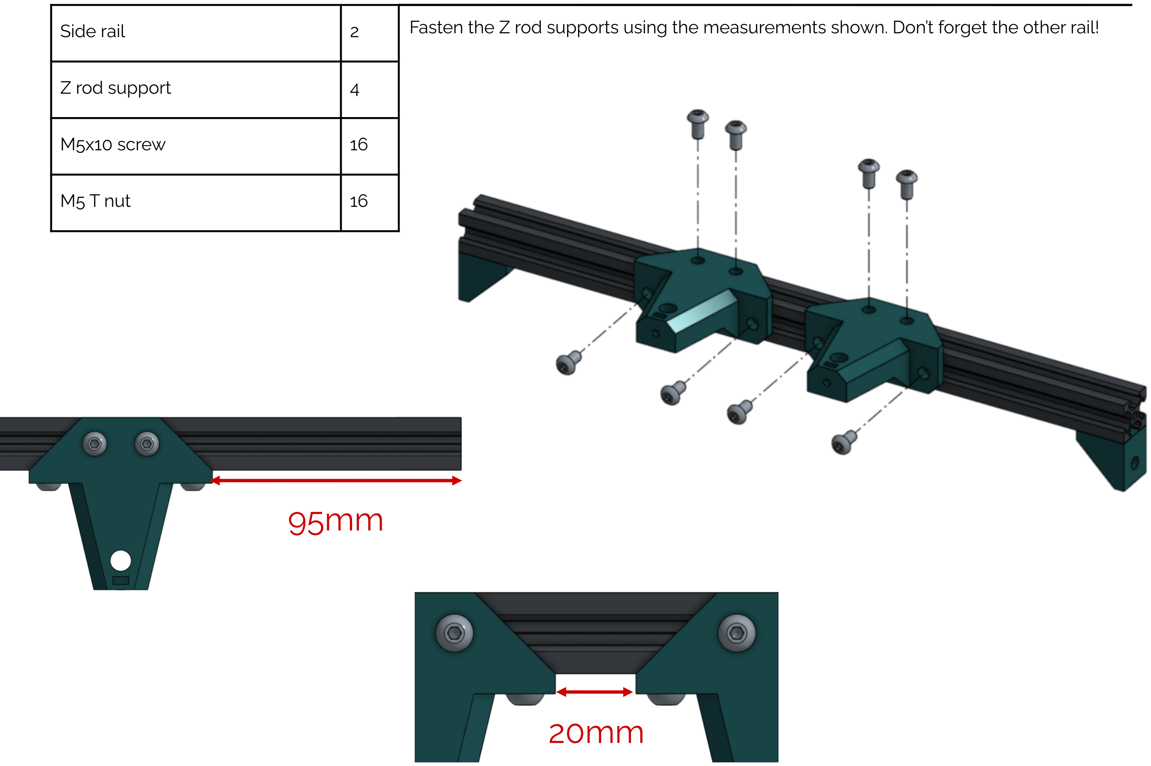
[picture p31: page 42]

Side rail | 2 | Fasten the Z rod supports using the measurements shown. Don’t forget the other rail!
Z rod support | 4
M5x10 screw | 16
M5 T nut | 16

95mm

20mm

Attach the two side rails using the measurements shown. The Z rod supports should fit over the rods. Don’t worry about being super accurate, the goal is to support the Z rods.

Side rail | 2
M5 T nut | 4
M5x10 screw | 4

105mm

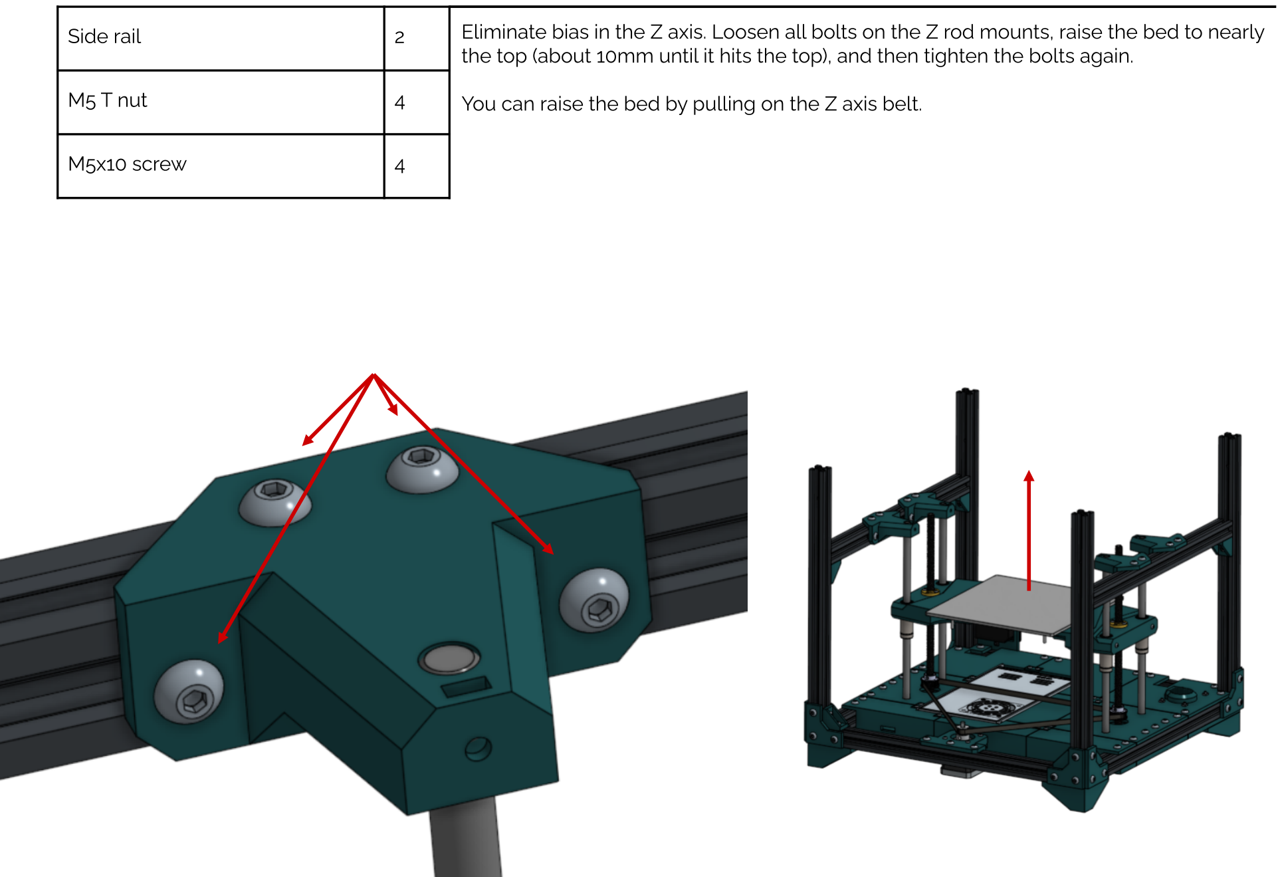
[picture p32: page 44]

Eliminate bias in the Z axis. Loosen all bolts on the Z rod mounts, raise the bed to nearly the top (about 10mm until it hits the top), and then tighten the bolts again.

You can raise the bed by pulling on the Z axis belt.

Side rail | 2
M5 T nut | 4
M5x10 screw | 4

M3 T nut | 4 | Clamp down the Z axis rods with M3 hardware.
M3x10 screw | 4

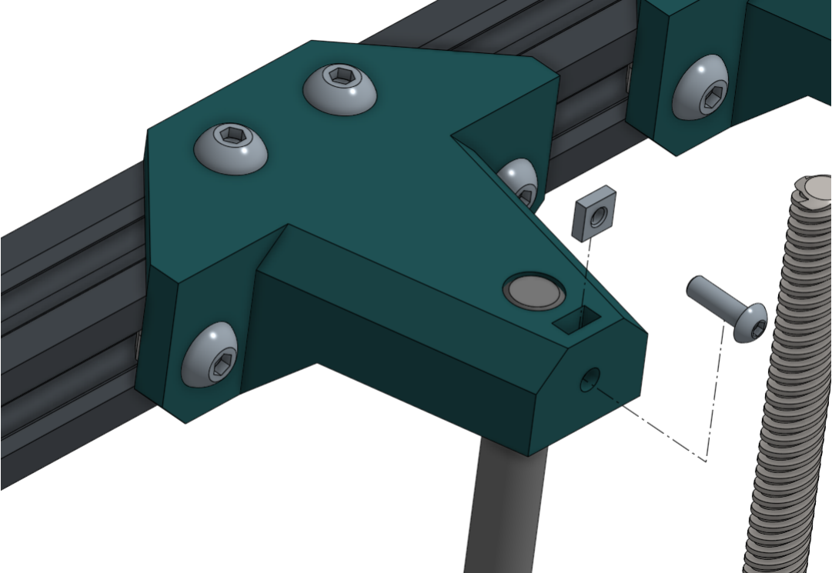
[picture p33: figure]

M5x10 screw | 4 | Fasten 4 plates to the top of the machine using the threads in each extrusion.
Fastening plate | 4

M5x10 screw | 8 | Complete the cube. Further reinforcement will be added later.
M5 T nut | 8
2020 extrusion | 4

Fasten long and short mounts to the corners of the machine. Ensure good alignment, it is critical for correct machine operation.
- Front left: Long
- Front right: Short
- Back right: Long
- Back left: Short
M5x10 screw | 8
M5 T nut | 8
Long mount | 2
Short mount | 2

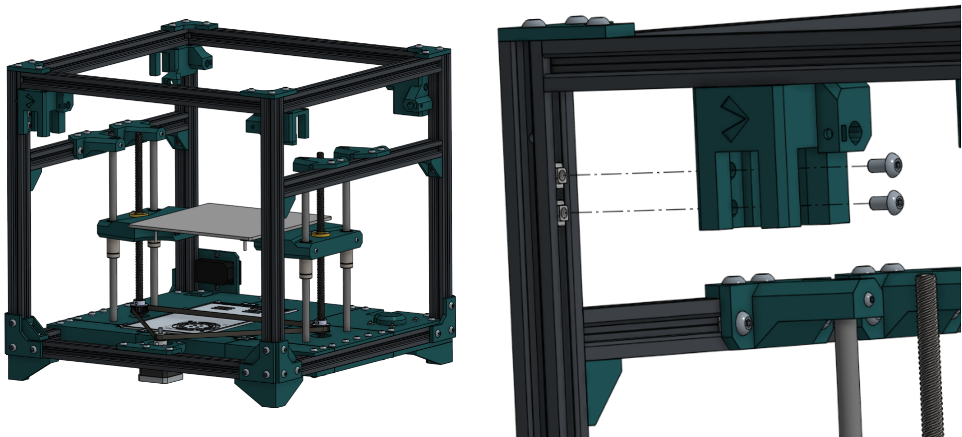
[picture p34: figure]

Each cross rod block requires a different configuration.
A. 1x standard block, bearing protruding right.
B. 2x standard block, bearing protruding left
C. 1x zip-tie block, bearing protruding left
M3x10 screw | 4
M3 square nut | 8
LM8LUU bearing | 4
Standard rod block | 3
Zip-tie rod block | 1

A

B

C

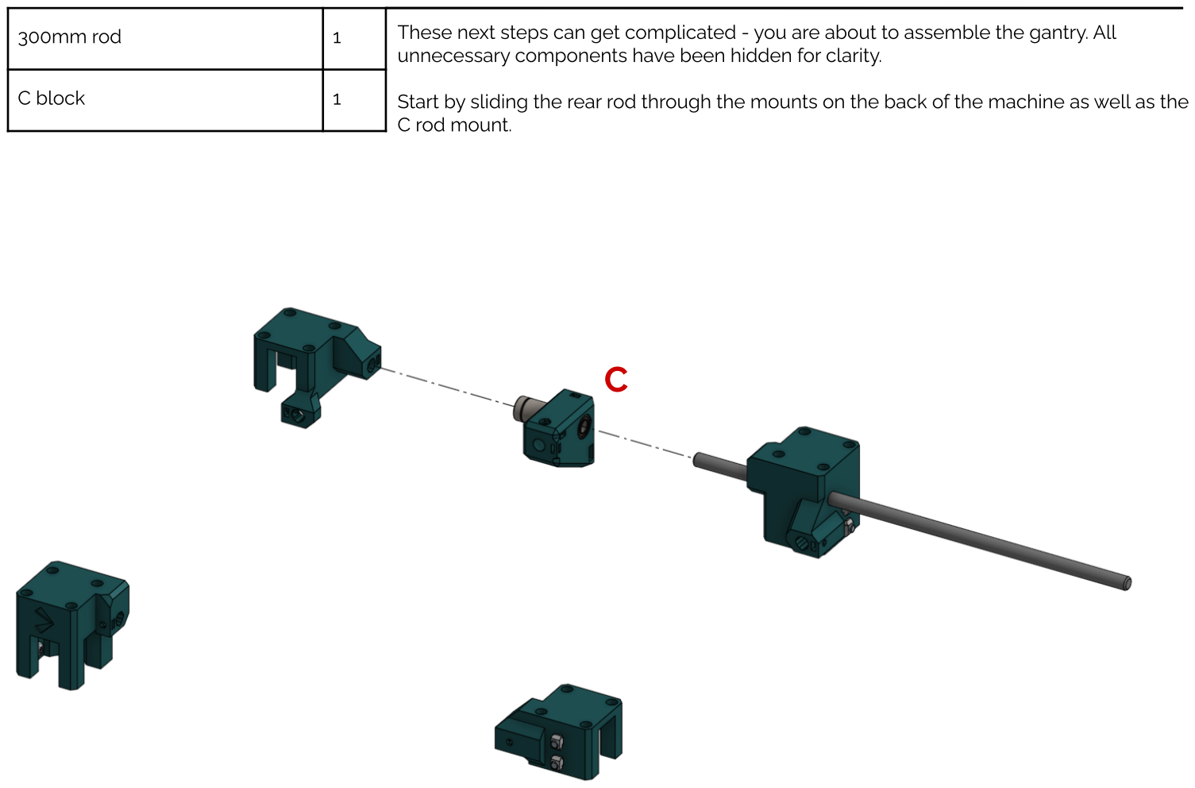
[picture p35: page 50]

These next steps can get complicated - you are about to assemble the gantry. All unnecessary components have been hidden for clarity.

Start by sliding the rear rod through the mounts on the back of the machine as well as the C rod mount.

300mm rod | 1
C block | 1

C

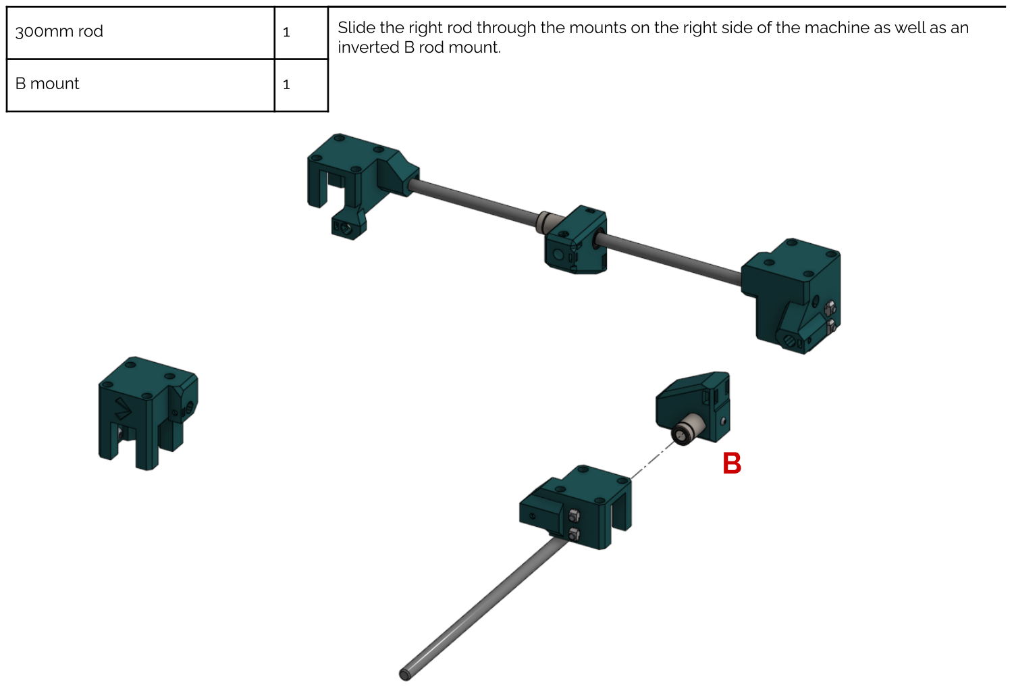
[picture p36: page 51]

Slide the right rod through the mounts on the right side of the machine as well as an inverted B rod mount.

300mm rod | 1
B mount | 1

B

Insert a rod directly into the C mount and slide the toolhead on. This setup is unstable, so
don’t let the toolhead slide off.

Toolhead designs may vary.

300mm rod | 1
Toolhead | 1

300mm rod | 1

B block | 1
A block | 1

B

C

300mm rod | 1

300mm rod | Everything should be fairly loose because there’s nothing clamping anything down yet. 1

Leave the machine and set up 4 motors. 2 of them should have the bottom of the idler nearly touching the motor face (or about 6mm from the top). The other 2 should have the tops of the idlers flush with the ends of the shafts.

The first motors (on the left) will be A motors, and the second motors (on the right) will be B motors.

Stepper | 4
Pulley | 4

Y

X

A motor | 2

Y

Y

B motor | 2

X

X

Plug in your motors once they’re all installed.

Secure the top of the frame using large corner brackets.

Small corner brackets cannot be substituted.

Large bracket | 4
M5x10 screw | 16
M5 T nut | 16

M3x10 screw | 4 | Use M3 hardware to clamp the cross rods in. There is a clamp on each block.
M3 square nut | 4

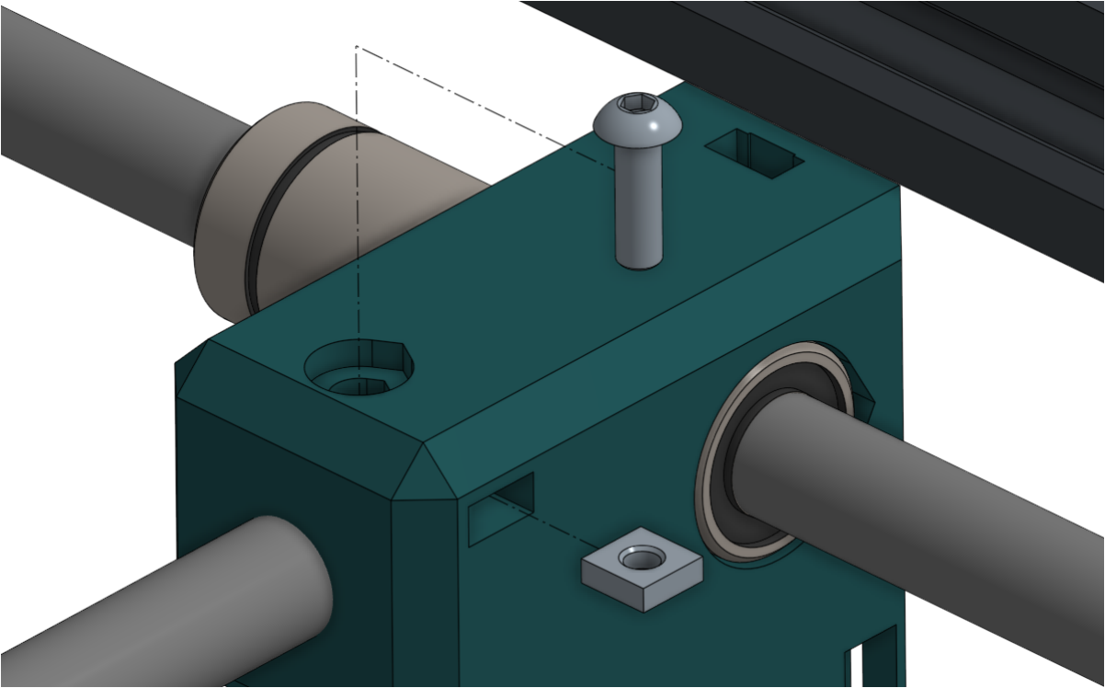
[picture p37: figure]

M3x10 screw | 8 | Use M3 hardware to clamp the gantry rods in. There are 2 clamps on each mount.
M3 square nut | 8

Assemble the 4 idlers with the idler pulleys, long bolts, and printed brackets. You do not need nuts, but you can install them if you want.

M5x30 screw | 4
Idler | 4
Idler bracket | 4

Install the idlers using the holes in the frame. Then, install the belts. Each side of the machine gets its own ~700mm belt, and each belt is terminated at the rod block by looping through the loops and binding it to itself using zip ties.

Once installed, trim any excess length coming off the rod block and tighten the belts by turning the screws.

Idler assembly | 4
M3x35 screw | 4
M3 square nut | 4
Belt | X
Zip tie | 8

M5x10 screw | 4 | Each idler gets an idler cover.
M5 T nut | 4
Idler cover | 4

Mechanical assembly complete.

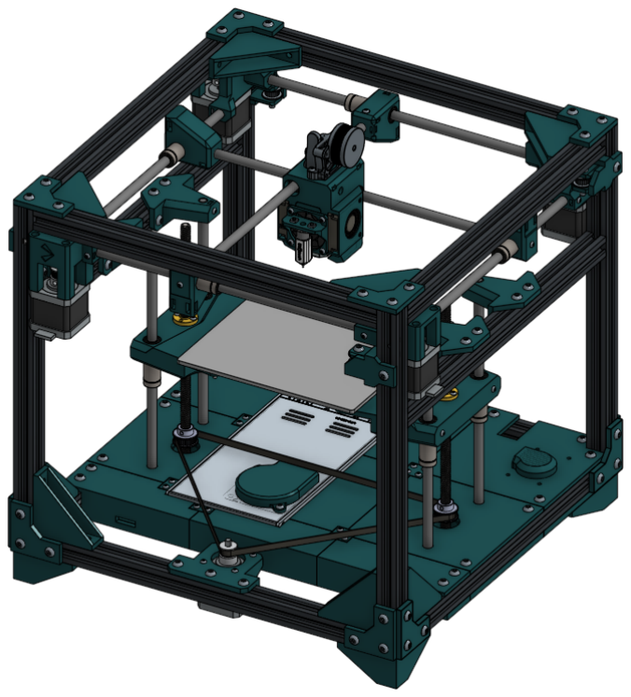
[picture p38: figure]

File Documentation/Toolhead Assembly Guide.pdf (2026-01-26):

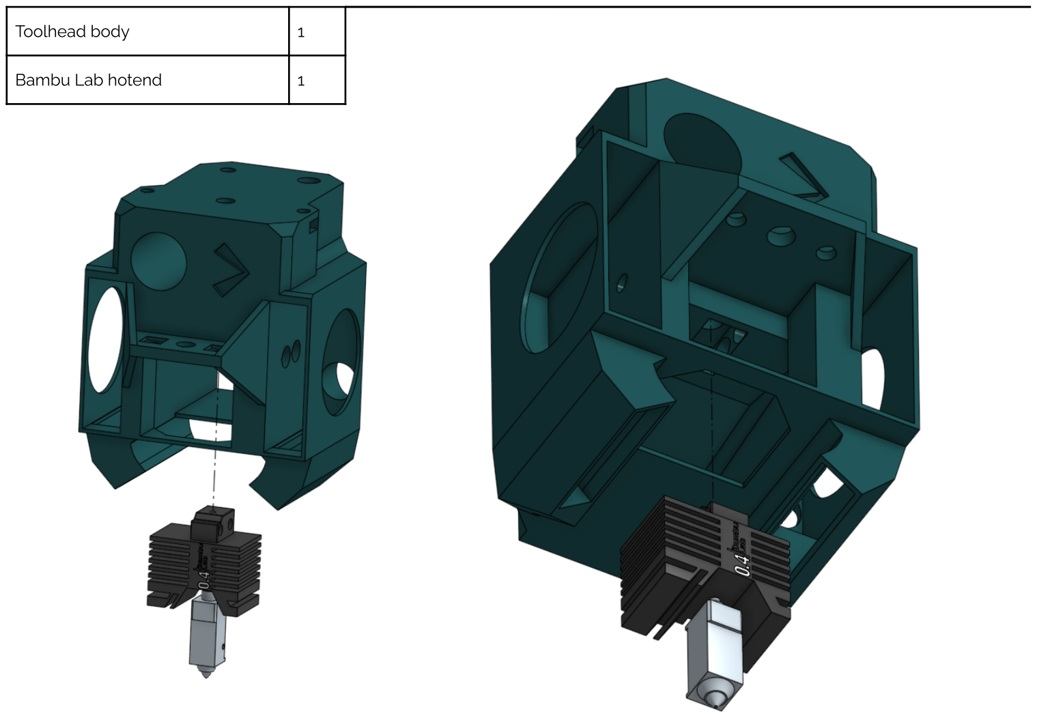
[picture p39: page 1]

Toolhead body | 1
Bambu Lab hotend | 1

Toolhead body

1

M3x20 screw

2

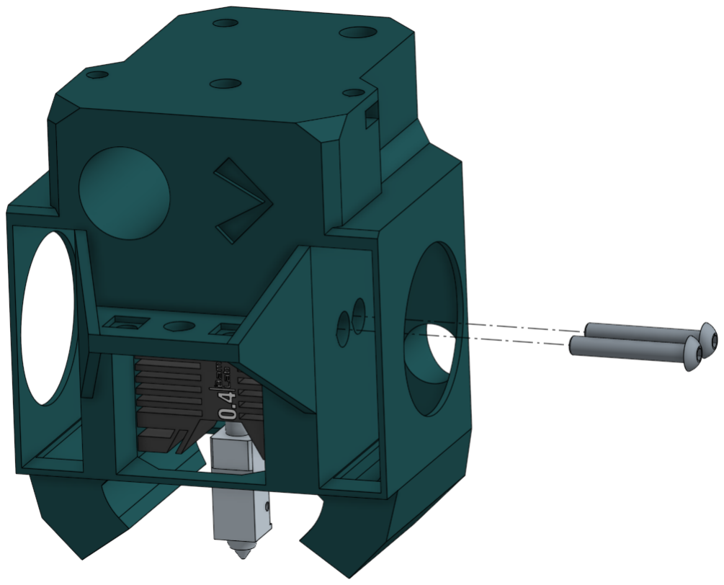
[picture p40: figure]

Toolhead body | 1
2510 fan | 1

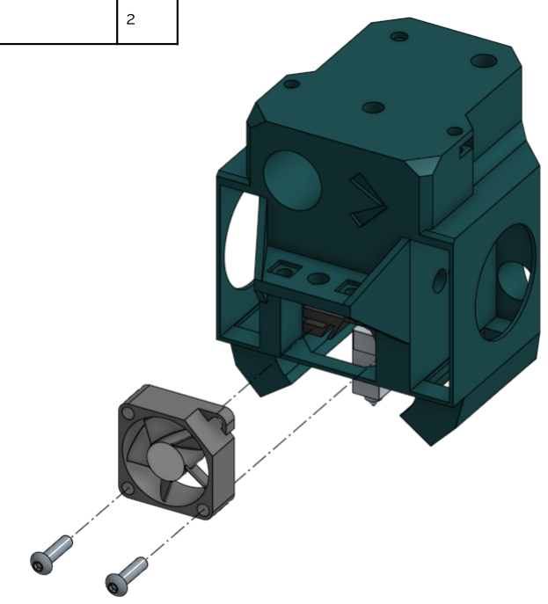
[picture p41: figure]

M3x12 screw | 2

Toolhead body | 1

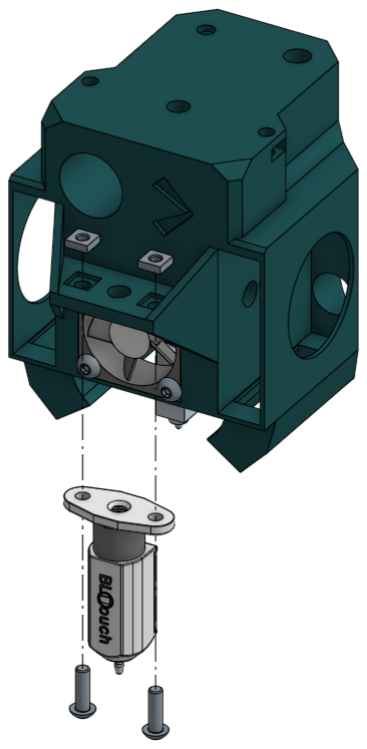
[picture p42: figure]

M3 square nut | 2
M3x12 screw | 2
BLTouch | 1

Toolhead body

1

4010 blower

2

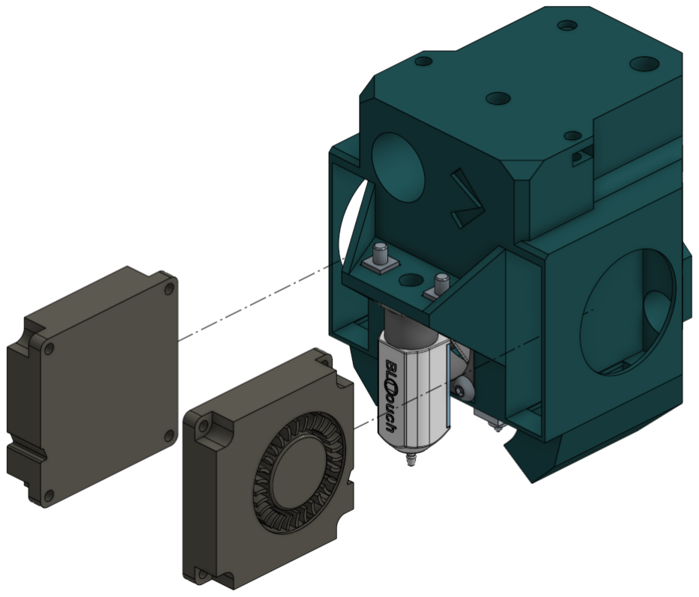
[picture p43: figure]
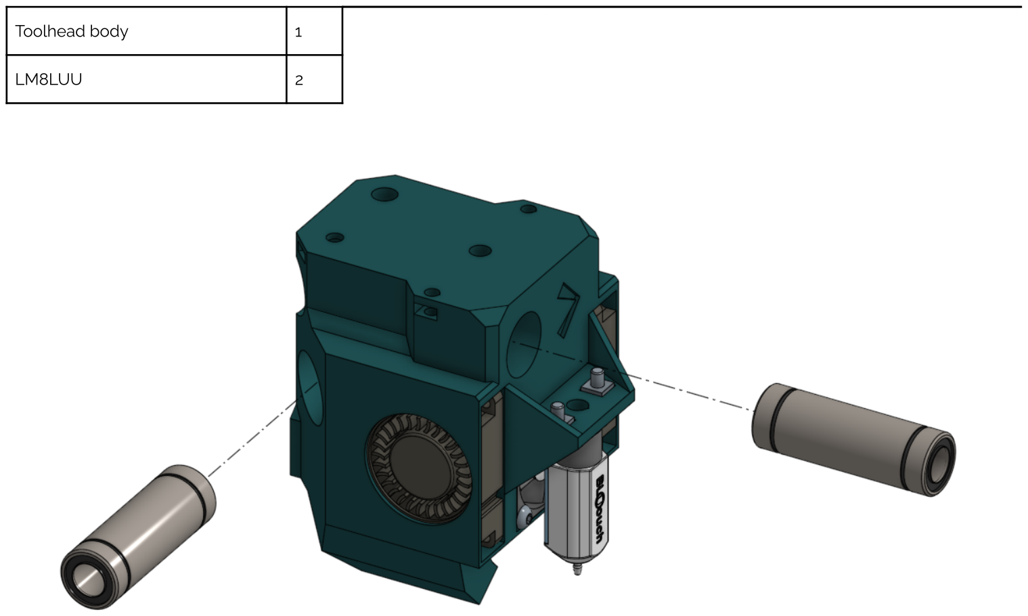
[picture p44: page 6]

Toolhead body

1

LM8LUU

2

Toolhead body | 1
M3x12 screw | 2

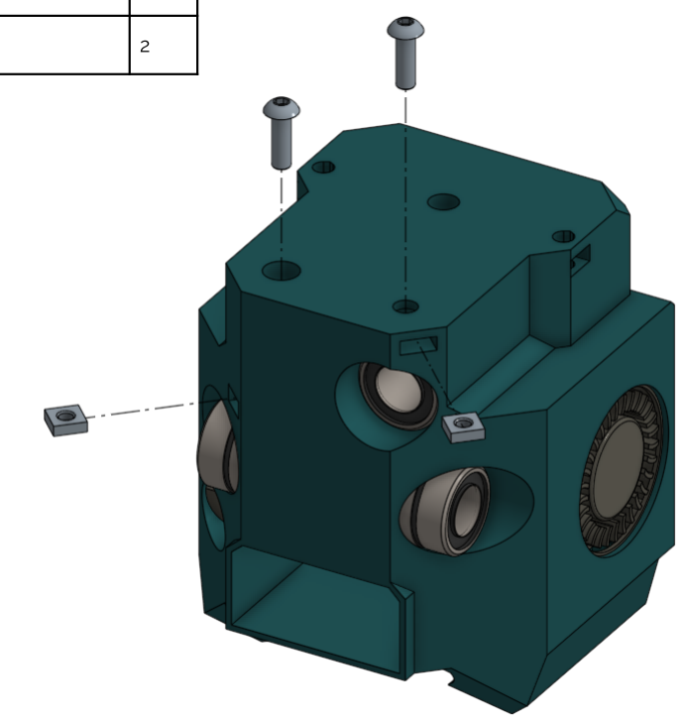
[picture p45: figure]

M3 square nut | 2

Toolhead body | 1

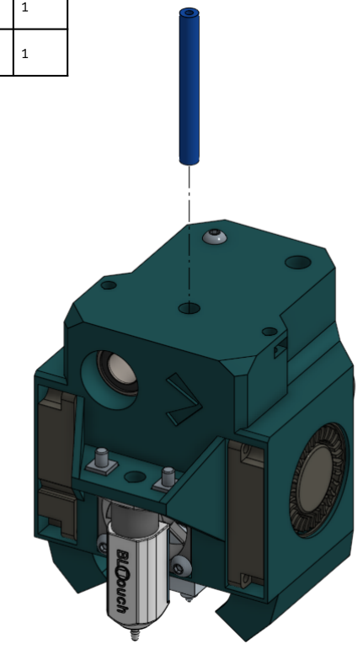
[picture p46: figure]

40mm PTFE tube | 1

Toolhead body | 1

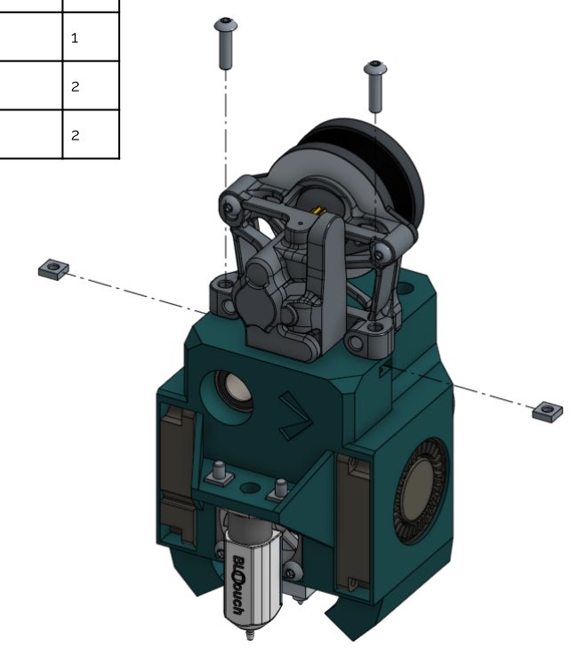
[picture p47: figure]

Sherpa Mini | 1
M3x12 screw | 2
M3 square nut | 2

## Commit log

2025-05-08 Add 3.0.5 Files
    [2x1 Screw Plate - 2mm.step, 2x1 Screw Plate - 4mm.step, 2x2 Screw Plate - 2mm.step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]
2025-05-08 add assy files and other bits
    [Corner Bracket.step]
2025-05-09 Update Printed Parts.md
2025-05-14 fix panels
    [Front Left Top Plate.step, Front Mid Top Plate.step, Front Right Top Plate.step]
2026-01-10 I sentence you to death for Z banding
    [Leadscrew Support.step]
2026-01-12 Create Corner Brackets.md
2026-01-13 sorry :/
    [Unicross 3 BOM.ods, Unicross 3 BOM.xlsx]
2026-01-26 new head!
    [BLTouch Mount.step, Bed Mount - Custom Unicross.step, Bed Mount - KP3S.step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]
